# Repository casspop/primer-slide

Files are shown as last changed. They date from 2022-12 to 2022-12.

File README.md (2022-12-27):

# primer-slide

## Hornady Lock N Load small pistol primer slide replacement

Typically the primer slide has little to no stress on it.  So it's rare for it to break.

When I added the PrimerCop to my press, the first version of the lower mount had a section that rubbed against the wheel on the primer slide as it went by to its lowest position during seating.  (The current version of that mount does not contact the wheel at all.)

It worked fine like that, but a friend of mine was seating his second primer, and was a little too aggressive with the handle as he pressed it forward.  The wheel caught the lower IR break-beam mount instead of rubbing.  The result was a broken slide.

The replacement was about $35.00 with shipping, so I decided I needed to see if I could make one myself.

This part is printed at a 0.10mm layer height with 100% infill using PLA.  It works perfectly.

I was able to salvage and use the shaft and wheel from the broken slide.

The 3D printed holes were all very close, and a drill bit finished them out perfectly.

I used a 1/4" endmill in my drill press at 300 rpm to mill out the groove in the top.  Without that groove, the bottom edge of the next primer up will grab the slide and prevent it from returning.

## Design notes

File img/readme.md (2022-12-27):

# Images

## Full resolution images are in this folder with no -s or -vs suffix.

### Click on these thumbnails for a larger image.

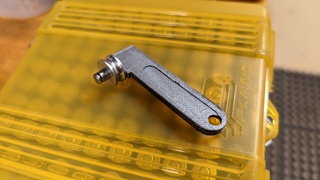
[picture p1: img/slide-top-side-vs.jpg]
Top Side View

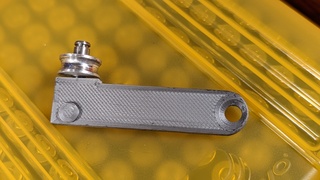
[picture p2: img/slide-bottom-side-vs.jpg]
Bottom Side View

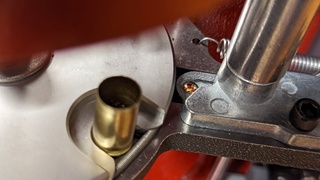
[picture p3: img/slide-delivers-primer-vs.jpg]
Slide Delivers Primer


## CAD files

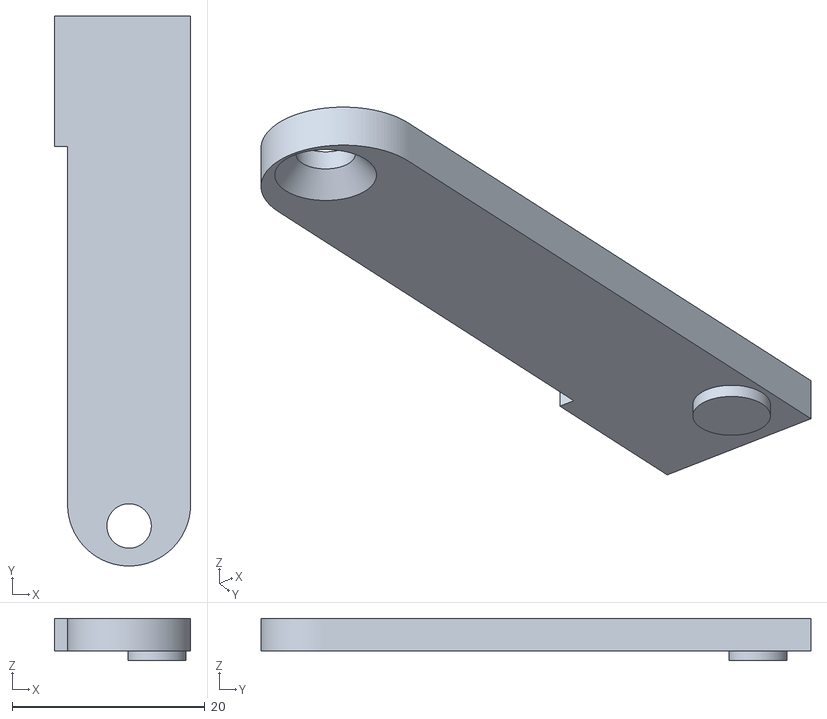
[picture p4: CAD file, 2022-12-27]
STL/horn_primer_slide.stl
14.1 x 57.0 x 4.40

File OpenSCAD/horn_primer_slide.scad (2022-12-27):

//horn_primer_slide.scad - Dr.Gerg's Hornady Lock-n-Load primer carrier slide
// OpenSCAD definition file
// https://www.drgerg.com
// printed in PLA at .10mm layer height with 100% infill.
//
// 12.75/2 = 6.375
//
//
$fn=128;
difference(){
    union(){
        difference(){
            difference(){
                union(){
                    translate([0,6.375,0])
                    cube([12.75,(57-(6.375)),3.4]);
                    translate([6.375,6.375,0])
                    cylinder(h = 3.4, d = 12.75, center = false);
                    };
                    translate([6.375,4.15,0])
                    cylinder(h = 10, r = 2.3, center = true);
                }
                translate([6.375,4.15,.5])
        cylinder(h = 8, d1 = 14, d2=0, center = true);

        }
        translate([-1.37,57-13.5,0])
        cube([14.12,13.5,3.4]);
    }
rotate([0,90,0])
translate([-1.7,57-6.5,-4])
cylinder(h = 10, r = 1.1, center = false); // 6.1 deep
}
translate([12.75-3.5,57-5.5,-1])
cylinder(h = 3.4, r = 3, center = false);
